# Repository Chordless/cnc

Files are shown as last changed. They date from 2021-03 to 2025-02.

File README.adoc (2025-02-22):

= The ERK-1 CNC
:toc: preamble

Designing, building & blogging a small desktop CNC.

.Current machine status
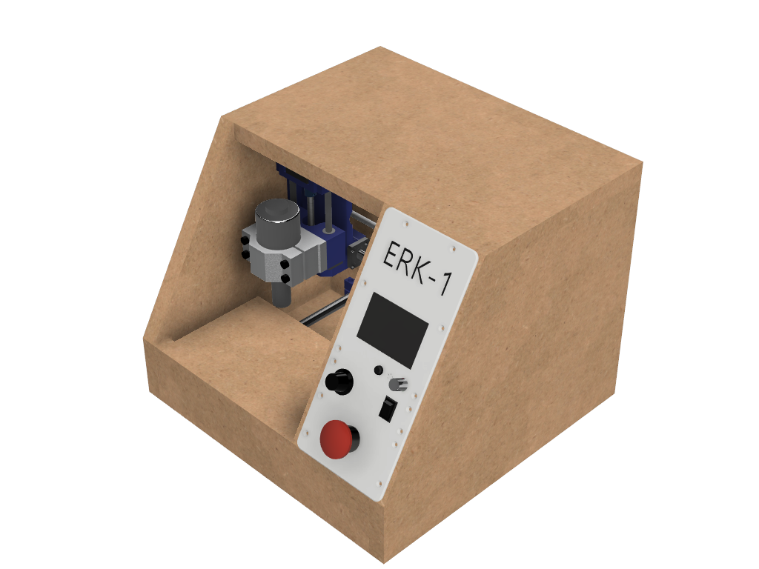
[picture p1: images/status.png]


== What's going on here then?
I'm designing a tiny desktop-friendly CNC. This repository will contain the design files, and I'm also blogging about the project in this readme file.

== Why yet another CNC design?
There are lots of great, free-to-build CNC designs already in existence on the internet. But, there is one particular type of CNC machine that I simply have not found any DIY designs for: The desktop micro mill. Think of those machines dentists use to create dental prostheses. Fully enclosed, tiny CNC machines you can use in an office: not too noisy, and not spewing dust everywhere. Something you could use while living in an apartment for experimenting and learning about CNC, and then being able to stow it away under the desk when not in use.

== Goals
* Apartment friendly
  - Quiet _enough_. CNC cutting will never be silent, but I'm trying to keep it quiet enough that the neighbors don't call the cops.
  - Dust control. CNCs can spew out lots of fine wood dust, and this would be terrible in an apartment. The machine must be fully enclosed, have controlled negative air pressure and a filter for catching all the dust. It needs something like a built-in vacuum cleaner.
  - "Stow-able". It should all be contained in a single unit, that you can pick up off the desk and stow in a closet. This also means it must be light enough that one person can feasibly carry it.
* Inexpensive
  - I'm going for a price of around 300-400$
* Possible to build without another CNC / Laser cutter. Some parts will unfortunately require a 3D printer. The machine frame will be mostly made out of wood.
* As small a footprint as possible. I'm inspired by the amazingly small https://vorondesign.com/voron0[Voron 0] 3D printer, but will have to scale up a bit from that ideal.

== Non-goals
* Metal milling
  - Out of the question. Nope. Not doing it. This will be a machine that can cut wood, plastics and modeling foam.
* Big working area
  - Not a goal at all. The machine footprint will be tiny in DIY CNC terms, and the cutting area will be even smaller. I'm totally fine with a toy-like working area of 13 cm x 10 cm x 2 cm.
* Precision
  - It would be nice if a tiny mill could mill tiny parts accurately. But this one won't. I'll be using cheap parts. Hopefully some of the parts can be "upgraded" for those with a larger budget, without requiring a redesign of the machine. Like using proper brand name linear bearings instead of the bottom dollar stuff I will be using. The bearing form factor will still be the same.

== Machine specs

- Fixed-gantry CNC machine
- Machine outer dimensions: 40 cm x 40 cm x 35 cm
- Axis travel: 130 x 130 x 60 mm (X, Y, Z)
- 200W spindle
- Sensorless homing, all directions (X-,X+,Y-,Y+,Z-,Z+)
- Fully enclosed
- Integrated dust filter

== Bill Of Materials

=== Frame and fasteners
- 8x different woods panels. Dimensions will come later. Should be cut out of 22 mm thick sheets of fibreboard or MDF. Any wood should work as long as it is 22mm thick.
- TODO: Lots of m3 and m4 bolts and nuts
- TODO: Wood screws
- TODO: Threaded inserts
- 2x 300 mm lengths of DIN rail (you can get away with using 240 mm)

=== 3D printed parts
- TODO

=== Electronics
- Controller board: `MKS GEN_L V2.1`
- Stepper motor drivers: 3x `TMC2209 V1.2`. These are silent, have software controlled current settings and support sensorless homing. With these, the machine won't need limit switches.
- Steppers:
  * 2x large `NEMA 17` stepper motors. The X- and Y-axis motors will be stationary, and they can be larger (longer) than the Z-axis motor.
  * 1x normal-sized `NEMA 17` stepper motor for the Z-axis. This will be moving as part of the X-carriage, so it shouldn't be too heavy.
- LCD screen: `RepRapDiscount Full Graphic Smart LCD Controller`
- Wi-Fi controller and web UI: A `Raspberry Pi` running chilipeppr, cncjs, or similar program.
- Spindle Motor: https://www.aliexpress.com/item/32908212687.html[Chinese 200W ER11 spindle with bracket]
- Spindle motor power supply. Normally rated for 48V max output, often sold as a set with the spindle motor. Should also include a potentiometer for adjusting motor speed.
- 12V Power Supply. 100W or greater. Powers the motion controller, stepper motors and fan.
- 12V 1A+ 60mm *strong* fan. You want a really strong fan. Example: https://www.aliexpress.com/item/32792312541.html[60 mm Fan]
- Emergency Stop Button, 22 mm: https://www.aliexpress.com/item/32885416975.html[E-Stop Button]
- KCD1-101 toggle switch: https://www.aliexpress.com/item/32627544552.html[Toggle Switch] (For turning the spindle on/off)

=== Linear Motion
* Z-axis
  - 2x LMK8LUU linear bearings
  - 1x T8 flanged brass nut  (2 Leads, Pitch 2 mm)
  - 2x 8x125 mm linear rods
  - 1x T8x100 mm trapezoidal leadscrew (2 Leads, Pitch 2 mm)
  - 1x 608ZZ ball bearing ("skate-bearing")
  - 1x Rigid shaft coupling, 5 mm to 8 mm
* X-axis
  - 4x LMK12UU linear bearings
  - 1x T8 flanged brass nut (2 Leads, Pitch 2 mm)
  - 2x 12x238 mm linear rods
  - 1x T8x232 mm trapezoidal leadscrew (2 Leads, Pitch 2 mm)
* Y-axis
  - 4x LMK12UU linear bearings
  - 1x T8 flanged brass nut (2 Leads, Pitch 2 mm)
  - 2x 12x258 mm linear rods (Axis length undecided)
  - 1x T8x252 mm trapezoidal leadscrew (2 Leads, Pitch 2 mm)

=== Misc
- A vacuum cleaner bag for `Philips Geneva HR6995`. If you use a different vacuum cleaner bag, you will have to design your own holder for it.

== Update 1 - 2021-03-18

.Humble beginnings
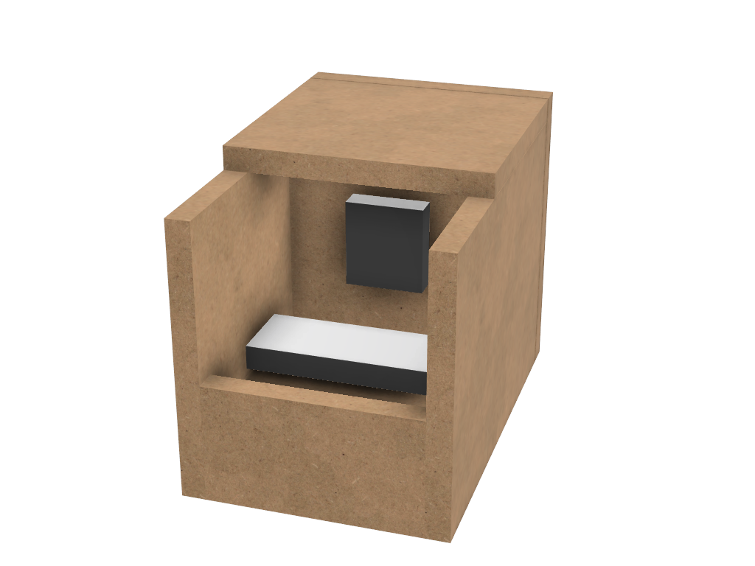
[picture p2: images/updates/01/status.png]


I've started sketching up the frame in Fusion 360. The rough design plan is:

- A cutting area in the upper front part of the machine.
  * Y-carriage moving from front to rear.
  * X-carriage moving from side to side
  * Z-carriage mounted on the X axis, moving up and down.
- A space under the machine for power-supplies etc.
- A space in the upper rear part of the machine for the motion controller and Raspberry Pi.
- A space in the lower rear part the machine for a powerful exhaust fan, and some kind of dust filter. Perhaps this will contain a vacuum cleaner bag, and literally work as a built-in vacuum cleaner.

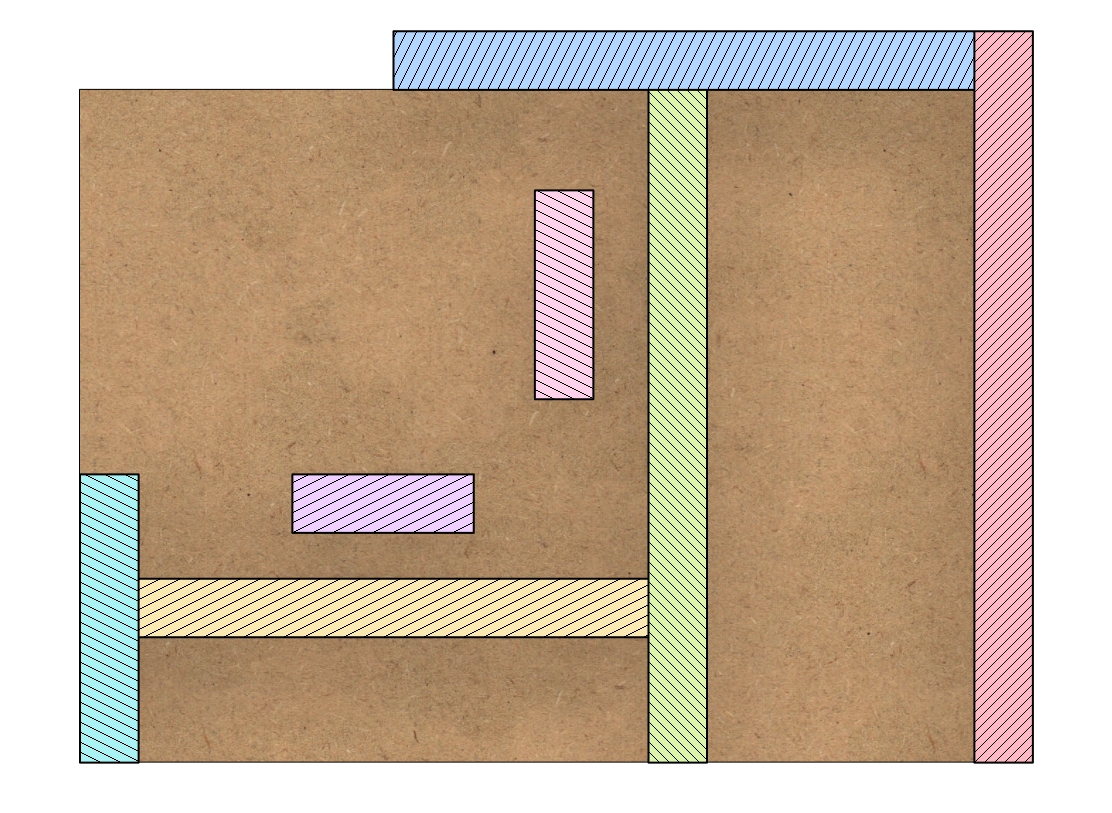
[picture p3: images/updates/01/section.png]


Eventually I realized that the shape and size of the frame is very dependent on the size and position of the spindle. I've made it my first goal to design the Z axis, and to make it as compact as possible. This will determine how small I can make the overall machine. As for the spindle, I'm currently designing for a 200W cheap chinese spindle motor. It seems small enough, yet should be able to cut small pieces of wood nicely.

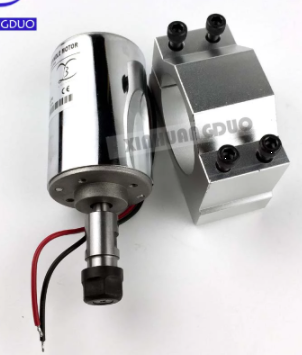
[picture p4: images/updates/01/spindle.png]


As part of the Z axis design, I'm making CAD models of some "standard" linear motion parts I expect to be using. I might even 3D print these models and use them as "mock" parts when prototyping the machine. I still haven't decided on the bearing form factors I will be using, and when I order them it will easily take one or two months before they arrive. Being able to assemble a "fake" version of the Z axis using plastic parts will probably be useful!

image:images/updates/01/LMK8UU v4.png[200,200]
image:images/updates/01/T8 Brass Nut v2.png[200,200]
image:images/updates/01/Spindle Clamp 52mm v2.png[200,200]
image:images/updates/01/Spindle 200W v2.png[200,300]

== Update 2 - 2021-03-19

.It's not easy being small
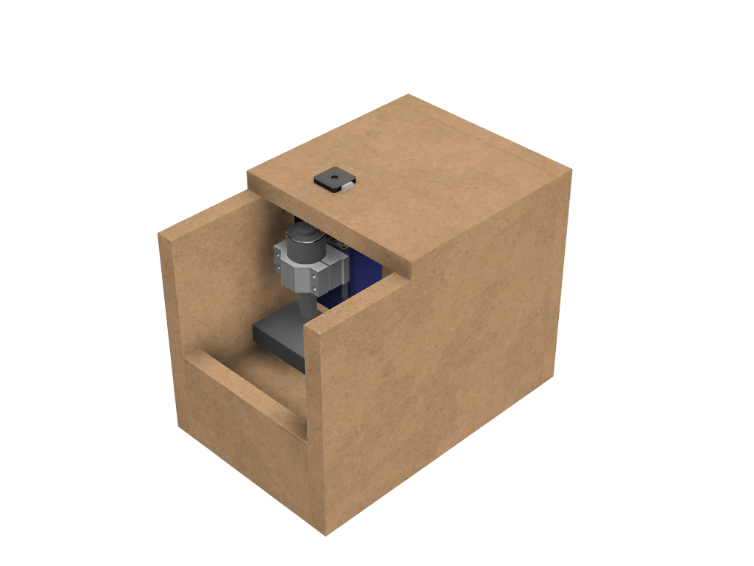
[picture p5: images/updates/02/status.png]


I've designed a first version of the Z-carriage and started on the X-carriage it rides on.
This machine is inspired by the tiny Voron 0 3D printer, which has _outside_ dimensions of 24 cm cubed. Right now my frame sketch has those _inside_ dimensions in the cutting chamber, so it's already larger than the Voron. And I've designed a Z-axis as small as I could without getting into weird tricks.

And yeah, that's the Z axis stepper motor poking through the top. _Oops._ I can expand the machine dimensions a bit more, but I don't want to go *that* big. I'll have to redesign these parts and save space wherever I can.

[discrete]
=== Z-carriage
The Z-carriage itself is pretty small. Most of it consists of the spindle mount bracket, and a small 3D-printed block to hold 4 bearings and a nut. If I'm sticking with a 52 mm diameter spindle, and the metal bracket, there's not much space that can be saved here.

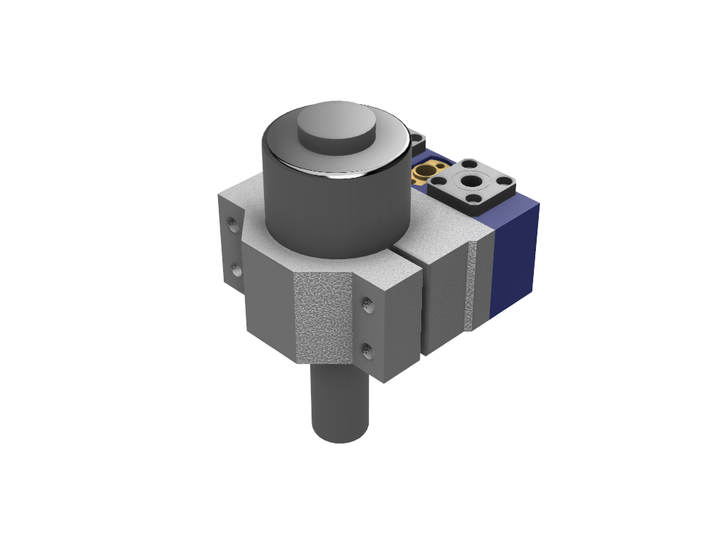
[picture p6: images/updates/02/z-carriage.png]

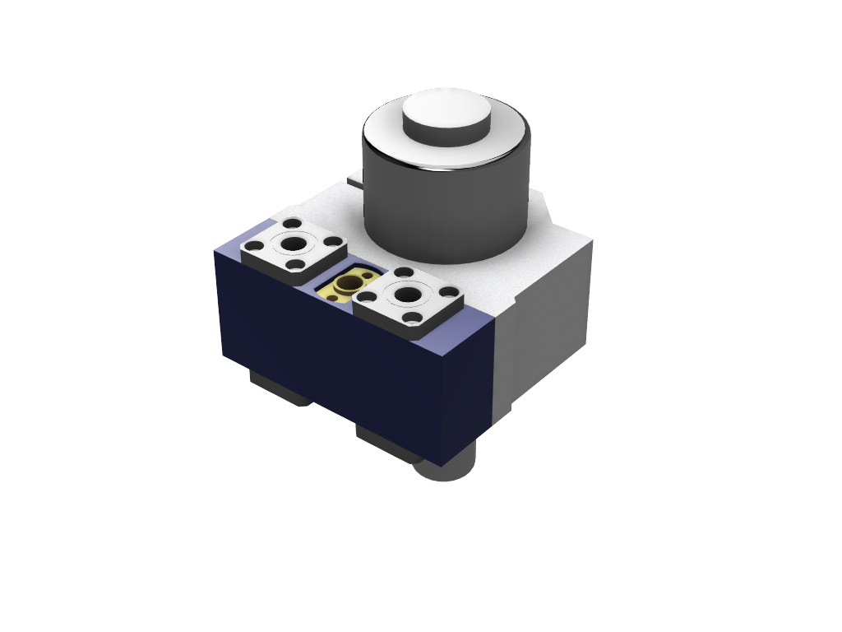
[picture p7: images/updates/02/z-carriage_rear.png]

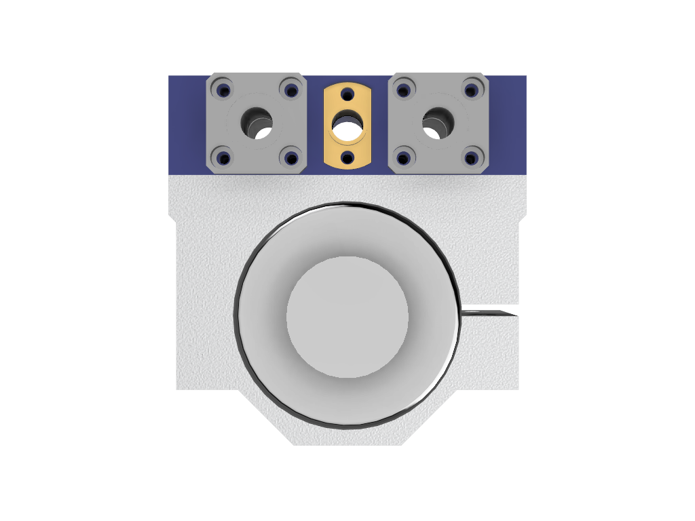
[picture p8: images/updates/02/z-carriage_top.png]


I actually don't want to use 3D-printed parts in this particular part of the machine. Anywhere but here. The spindle can get pretty hot, and that heat will creep into the 3D-printed block. I don't want to worry about my machine parts melting when I use the machine, so I'll have to pull some tricks here. Perhaps I can design in a sheet of plywood between the aluminium bracket and the 3D-printed block, as thermal insulation. We'll see.

[discrete]
=== X-carriage / Z-axis
The first X-carriage design is a simple box made from 3D-printed parts.
(The stepper motor and coupling don't quite line up with the brass nut in the z-carriage. I'll rework it later.)

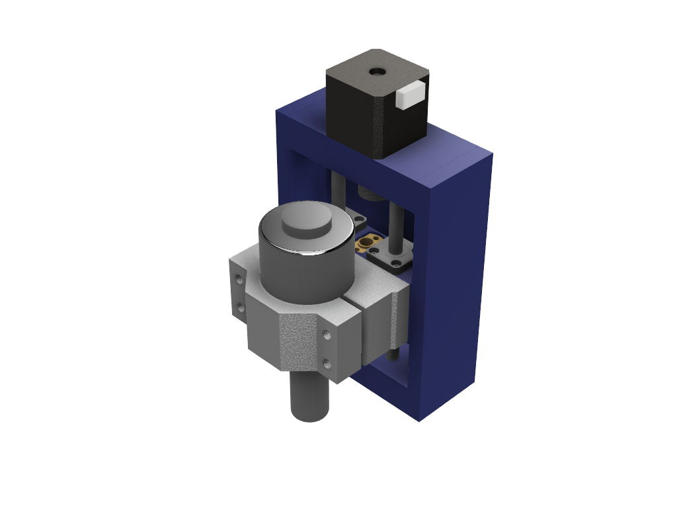
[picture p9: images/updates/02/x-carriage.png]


There's probably a bit of space to save here.

- The box sides aren't _necessary_. They do help with rigidity though.
- Perhaps the axis could be folded, using a belt drive, so that the stepper motor isn't on top. I don't know where else I want to put it though.
- The whole axis could be made shorter.

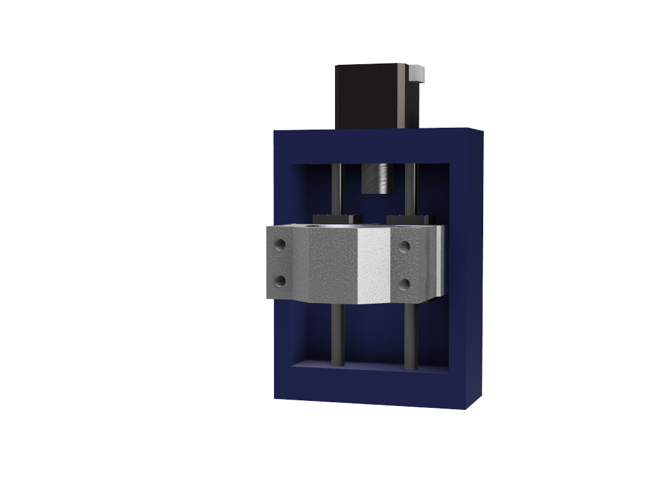
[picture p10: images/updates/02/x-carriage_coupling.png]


In this image, the axis is all the way up, at the end of it's 40 mm travel. The stepper motor shaft and coupling make me waste quite a lot of space. Without those, the box could be shortened, so the Z-axis bearings touch the top of the box in this position. If I choose a stepper motor with an integrated 100 mm leadscrew, instead of a regular shaft, I can save 30 mm of height here. That's probably too good to pass up.

== Update 3 - 2021-03-22

.Redesigned Z-axis
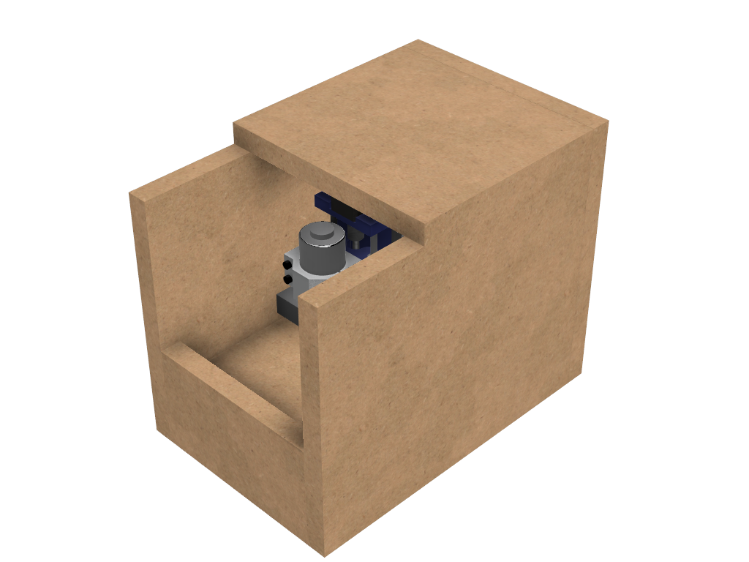
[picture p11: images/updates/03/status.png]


I managed to improve the Z-axis and shrink it down to something usable. I still had to increase the height of the machine a bit, but not that much.
Before and after shots of the Z-axis:


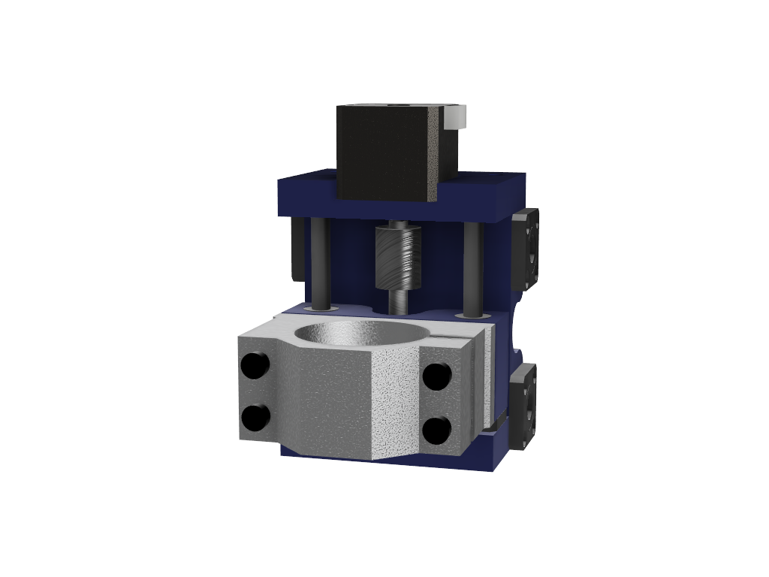
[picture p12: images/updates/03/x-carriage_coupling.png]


The images are not to scale, so it's not a perfect comparison. The box has been shortened a lot, and the plastic sides are gone. I added clearance for the stepper motor coupler to the Z-carriage part, so I don't have to use a special stepper motor with an integrated leadscrew after all. The Z-carriage now moves all the way up, so it touches the plate holding the stepper motor, and axis travel is still 40 mm.

The Z-axis and X-carriage is now complete, so I will print this version and see if things fit together as planned.

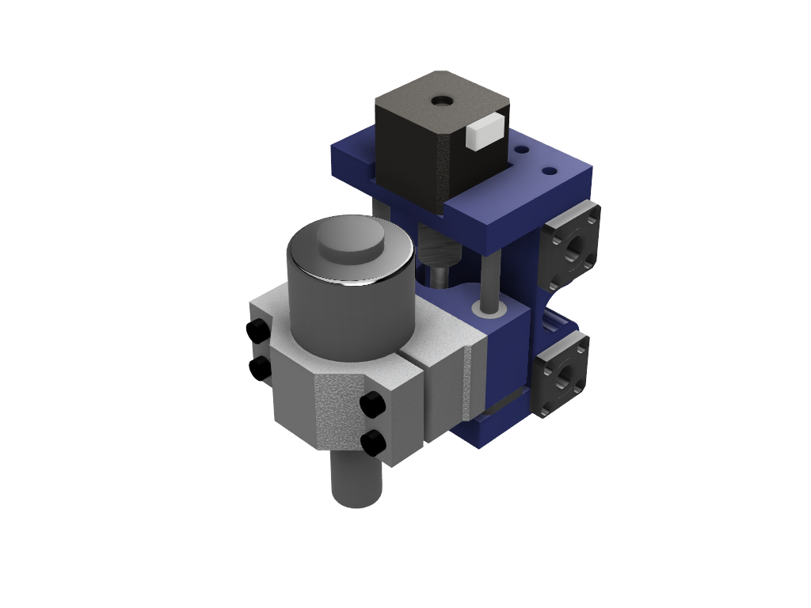
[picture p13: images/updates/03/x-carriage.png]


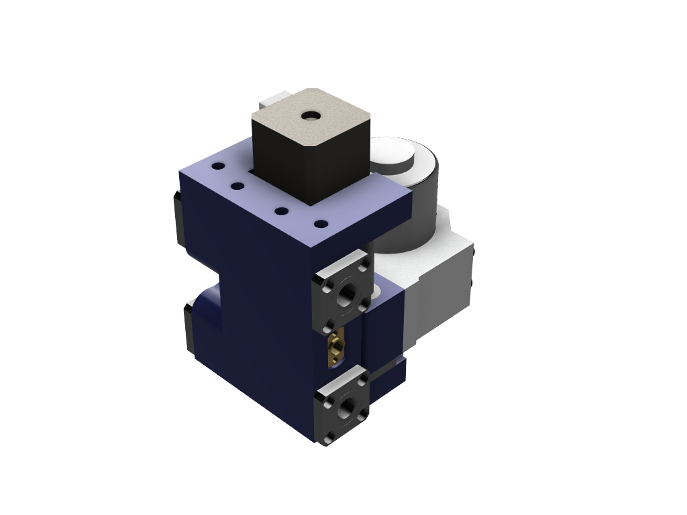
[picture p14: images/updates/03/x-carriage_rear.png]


I will also be liberally using "mock" parts for this test assembly, since no linear motion parts have been ordered from ebay yet. A bunch of more standard parts were modeled:

image:images/updates/03/mocks/608ZZ Bearing v2.png[,150]
image:images/updates/03/mocks/Flexible Coupling v2.png[,200]
image:images/updates/03/mocks/LMK8LUU v2.png[,250]
image:images/updates/03/mocks/LMK12UU v2.png[,270]
image:images/updates/03/mocks/NEMA 17 37mm v4.png[,300]
image:images/updates/03/mocks/NEMA 17 60mm v2.png[,300]

The next step of the design is to revisit the machine frame. I want to make some layout changes before properly designing in the X-axis.

== Update 4 - 2021-03-25

.Redesigned frame
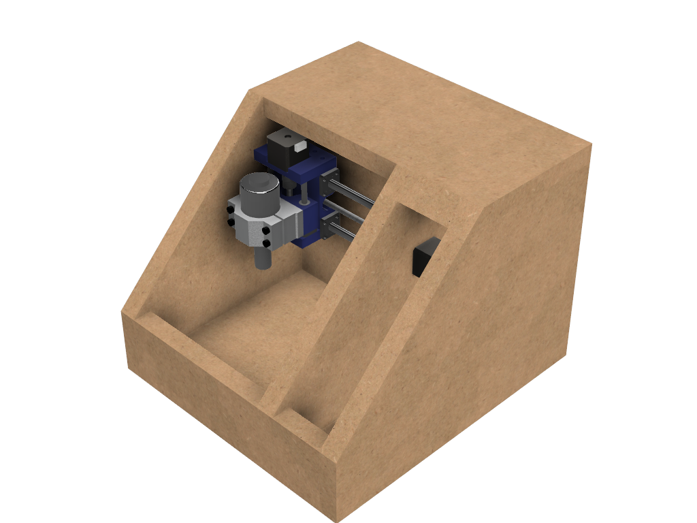
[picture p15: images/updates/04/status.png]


The frame has been redesigned, now it looks more like a usable machine. I plan to have a hinged plexiglas cover in front of the cutting area, and a 3D-printed panel on the right side. The right side panel will hold the LCD-display, emergency stop button, and probably a spindle speed control knob.

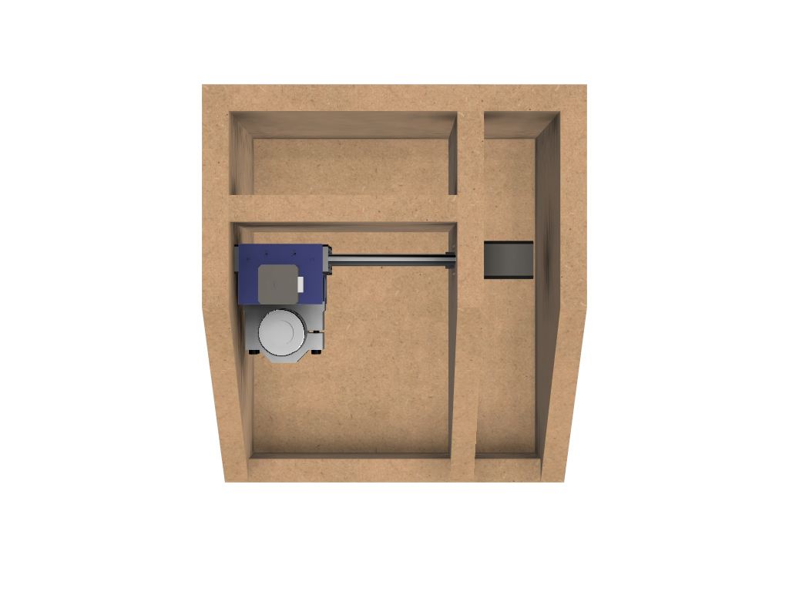
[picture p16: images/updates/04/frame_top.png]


The frame plan changed a bit:

- The cutting chamber is still on the front left side.
- There's no longer a power-supply chamber under the machine.
- The whole right side of the machine is now the electronics compartment.
 * (Hopefully I can fit all the controllers and power supplies here.)
- There is another chamber behind the cutting area, that I plan to use for dust management (an integrated vacuum cleaner).

Outside dimensions at this point are:  +
40 cm x 44 cm x 34 cm (width x length x height)

There is also now a complete X-Axis. The rods are held in halfway-trough drilled holes in the wooden side panels. I am unsure if this is a good idea, or if I should design some actual holders for the rods, that then bolt onto the side panels. On the other hand, that would eat up a couple centimetres of X-axis travel.

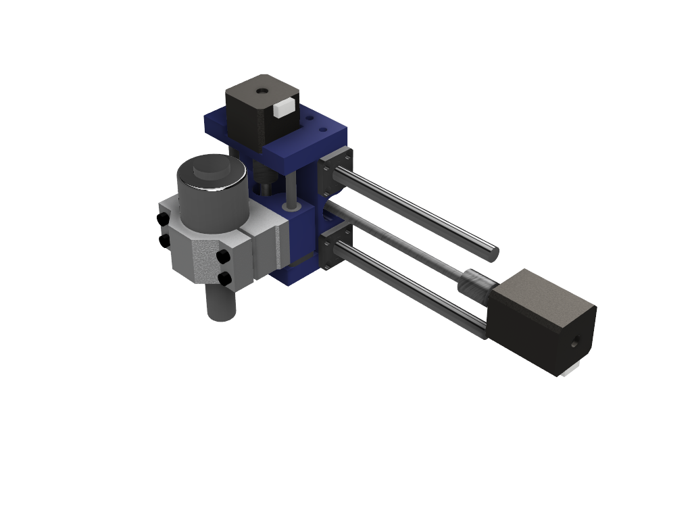
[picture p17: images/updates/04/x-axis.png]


Next step: The Y-carriage

== Update 5 - 2021-03-29

No real design update today. The Y-axis is in progress. I'll just be writing about electronics and 3D printed prototyping since I think it's neat.

[discrete]
=== Electronics
These are the motion electronics I plan to use (disregard the blue lab power supply at the top):

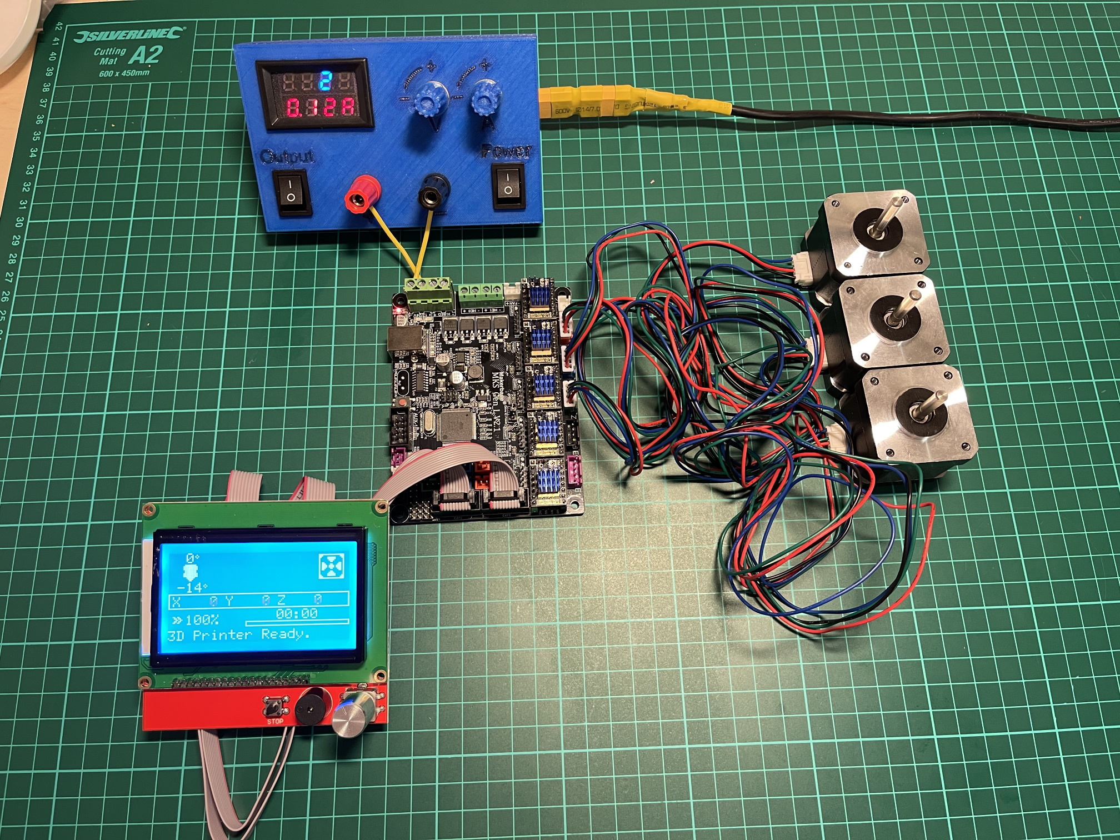
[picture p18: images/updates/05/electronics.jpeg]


The controller board is the `MKS GEN_L V2.1`. It's based on the 8-bit ATMEGA2560 CPU, quite common among 3D printer controller boards, and has nice inputs and outputs for the common things a 3D-printer needs. It's also quite easy to repurpose for driving a CNC.

The stepper drivers I am using are the `TMC2209`, and they should be very good in combination with this board. For one thing, the drivers make the steppers move very quietly. The stepper motor noise is not much compared to a cutting tool driving through wood, but every little bit helps. The board supports communicating with these drivers over UART, so the board can send configuration commands to the drivers, and get status updates in return. This lets us configure the stepper motor current in the firmware. For example, we can set the current of each driver to exactly 1400mA, instead of fiddling with a tiny potentiometer to try to achieve a similar result.

The stepper drivers can also tell the firmware when motors are unable to move as commanded; when they lose steps. This means we can let the machine home itself without using any limit switches. We just tell the machine to move as far as possible along, say, the negative X-axis. When the machine hits the end of its travel, the motors will stall, and the stepper drivers will let the controller board know. We can then mark the current X position as X=0. This also lets us do the same thing for the positive X direction, and the same for the Y-axis and Z-axis. This is normally not supported on such machines, as positive homing would require 3 extra limit switches, in addition to the regular 3 switches used for homing each axis to zero.

The plan is to use this for usability improvements in the machine. Like automatically homing each axis to the positive direction after a cutting job. This would move the spindle up and to the right (out of the way), while pushing the Y-carriage towards the user. Which is nice.

[discrete]
=== Prototyping
I have printed a prototype of the Z-carriage and X-carriage. The parts printed in white are "real" machine parts; I intend for these to be 3D-printed in the final machine. The blue parts are just stand-ins; these are supposed to be standard linear motion parts that will be ordered when the machine design is complete. I already had these modeled to help with the CAD design of the machine, so it didn't take much extra work to get them 3D-printed.

.Z-axis all the way down
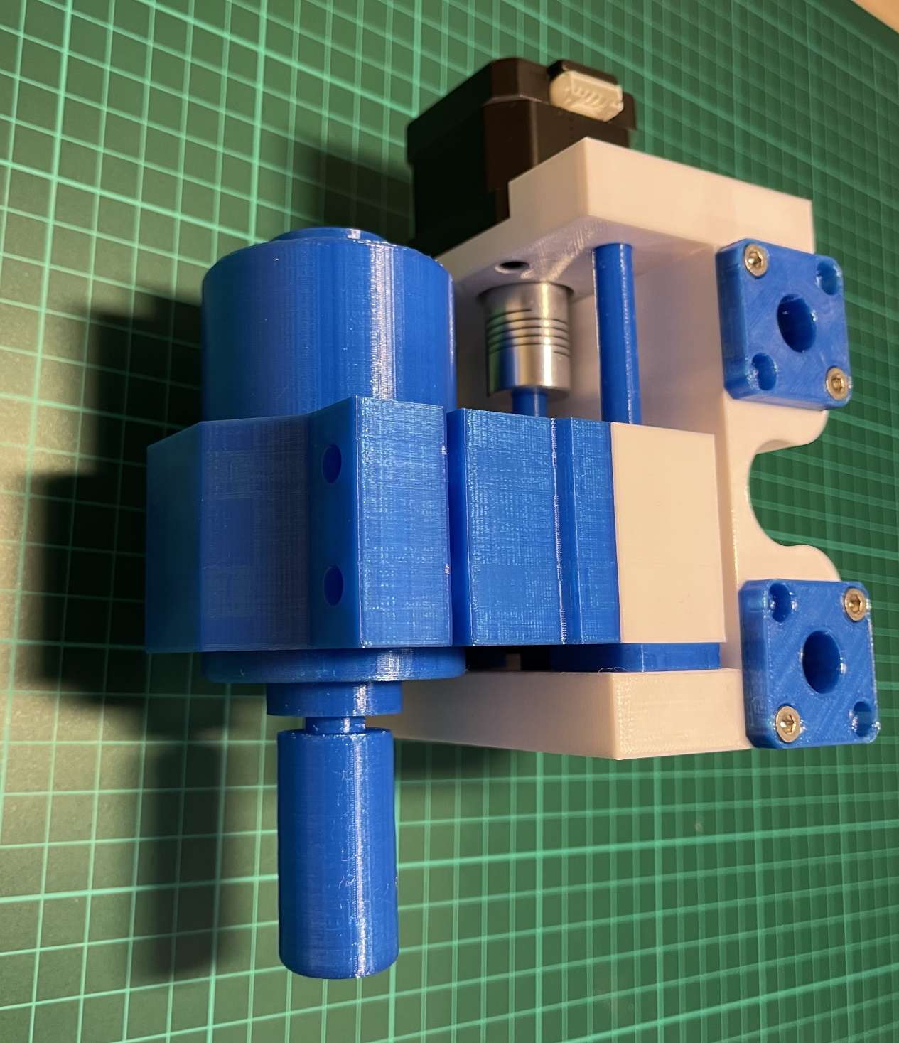
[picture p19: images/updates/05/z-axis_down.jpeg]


.Z-axis all the way up
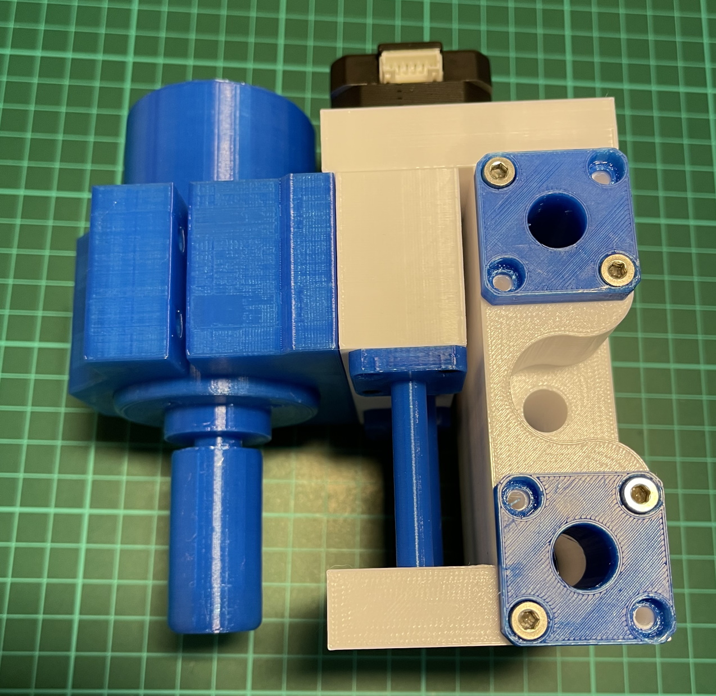
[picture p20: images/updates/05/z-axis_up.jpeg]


.Z-carriage with mock spindle and motor mount
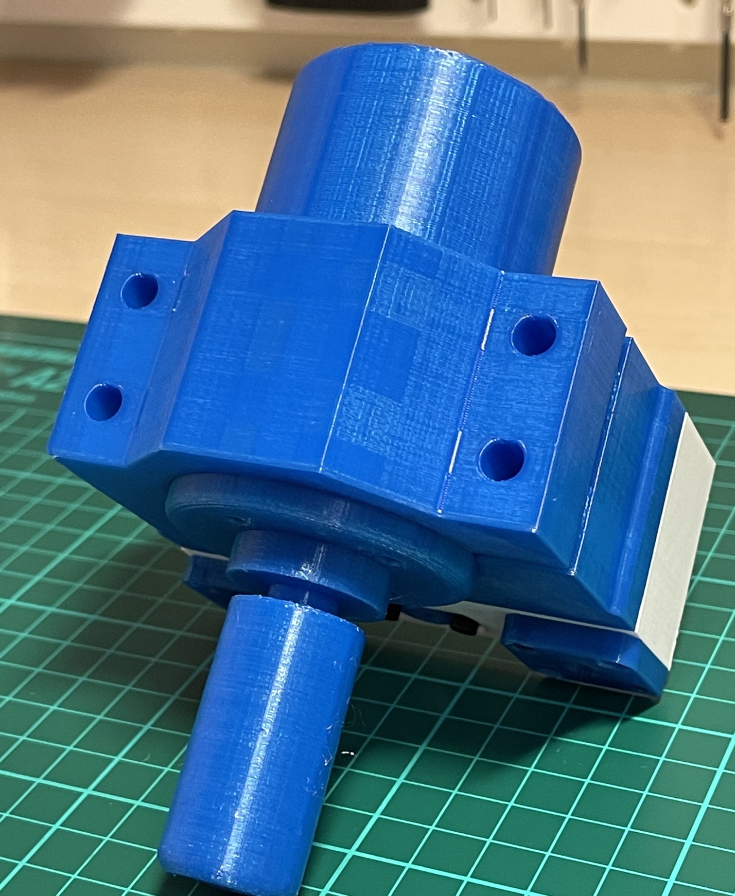
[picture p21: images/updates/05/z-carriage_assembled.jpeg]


.Z-carriage with mock spindle and motor mount, disassembled
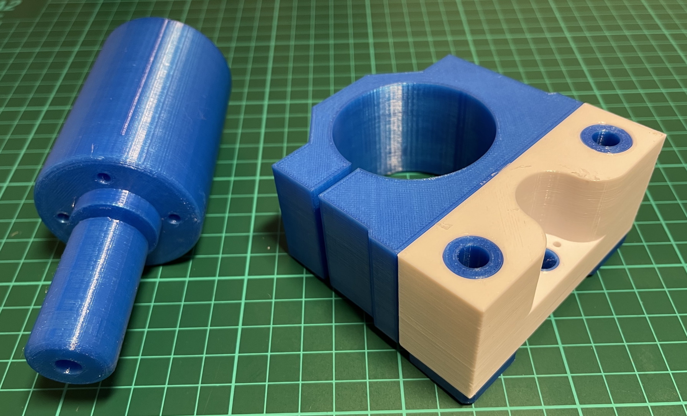
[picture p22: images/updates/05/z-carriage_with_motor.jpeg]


Prototyping like this is not only *fun*, but also lets me get a feel for the assembly of these parts, and catch problems early. Assembly went ok this time, there were no inaccessible screw-holes or such things. I found a few things I want to change though.

The current X-carriage consists of two parts: A large base part, and a top plate (holding the stepper motor) that screws into it from the top.

.Full Z-axis (Z-carriage and X-carriage)
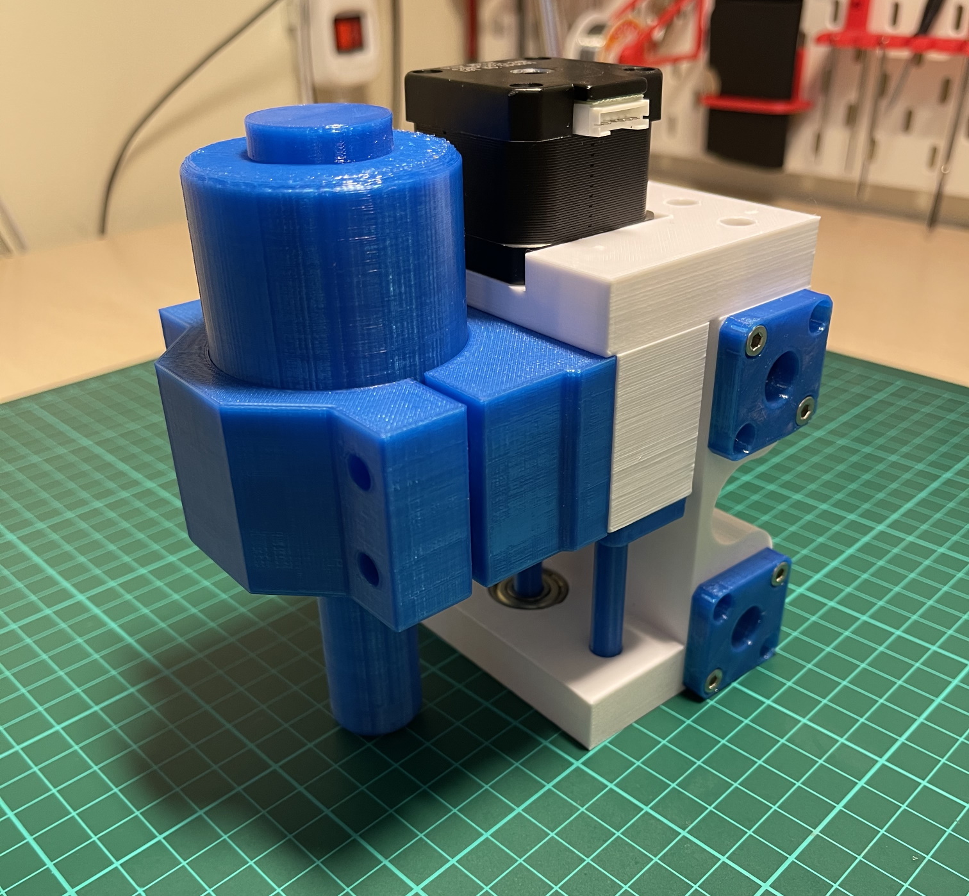
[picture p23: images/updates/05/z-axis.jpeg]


I was hoping the screws would hold these two pieces tightly together and in alignment. After seeing it in real life, I don't think the screw connection is strong enough. I will probably redesign the X-carriage to be a single part. This also lets me push the top X-rail higher up on the X-carriage, giving a longer distance between the X-axis rails. This is generally a good idea, mechanically.

I also think I can save a centimeter or two in the width of the X-carriage. The width of the Z-carriage is more or less defined by the width of the motor mount; this doesn't need to carry over to the X-carriage. At the very least the linear bearing flanges don't need to stick out of the sides of the X-carriage. This gives less distance (left to right) between the X-rail bearings, which is not a good idea mechanically. The upside is that it would give me more X-axis travel without increasing the width of the machine.

== Update 6 - 2021-03-31

.All 3 axes designed
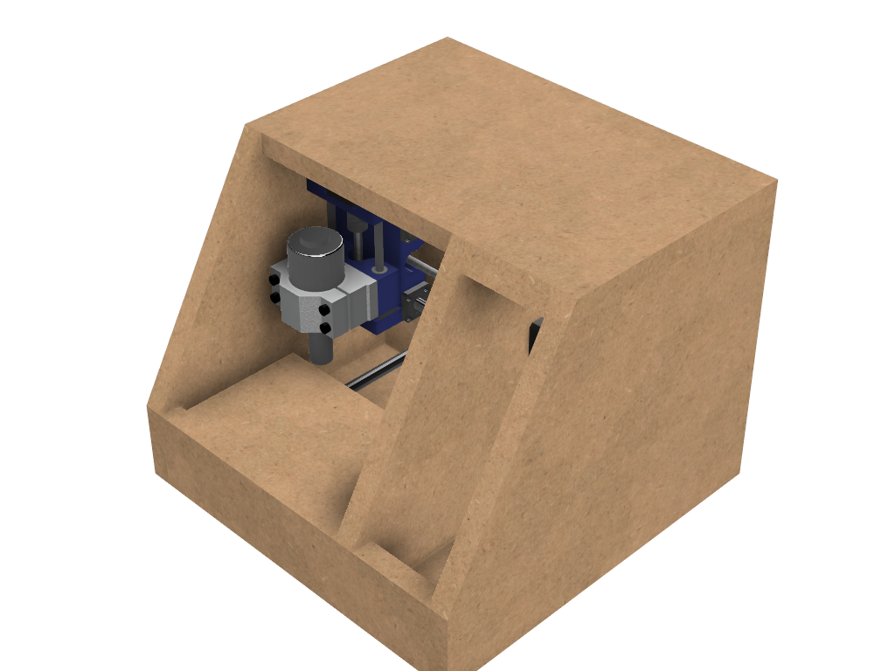
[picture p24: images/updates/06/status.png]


The machine now has a Y-carriage and Y-axis! Once all the three axes were in place, lots of small adjustments happened.

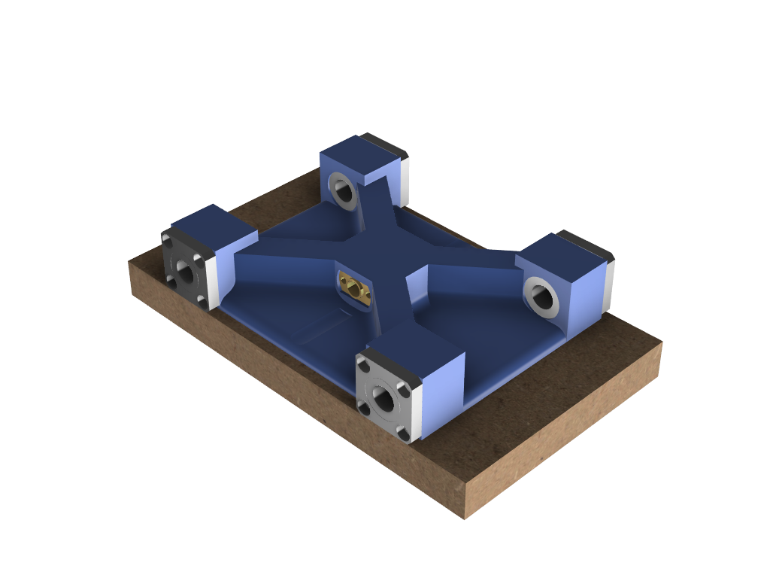
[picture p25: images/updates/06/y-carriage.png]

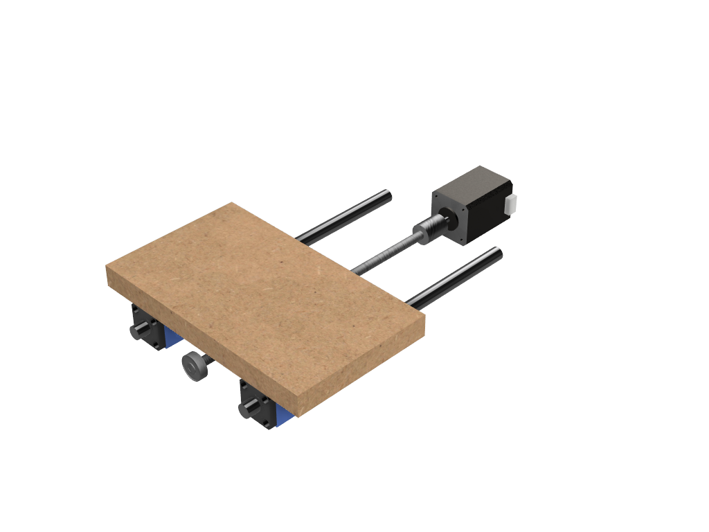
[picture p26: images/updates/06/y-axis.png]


- The X-axis was aligned, so the cutting tool is in the middle of the Y-axis.
- The angle on the front of the frame was changed from 45 deg to 30 deg. The top of the spindle motor could collide with the front plexiglas without this change.
- I also increased the Z-axis travel from 40 mm to 60 mm. This is just to ensure the Z-axis has enough clearance, even when using long or short cutting tools. In practice the thickest material you will be able to work with is still only 20-30 mm.

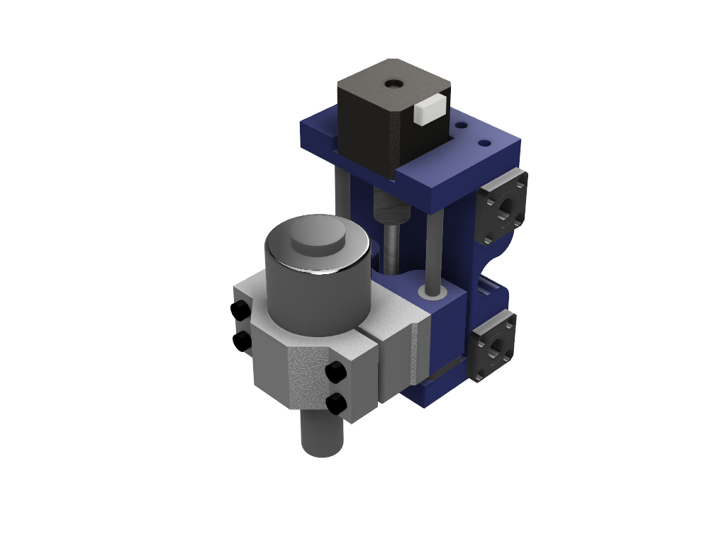
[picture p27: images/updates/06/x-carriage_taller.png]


So far I've been designing the frame with a 28 mm material thickness. The MDF wood sheets I will be using are actually 22 mm thick, so I updated the model to match this. The machine outer dimensions became slightly smaller as a result. Right now the machine dimensions are 396 x 396 x 324 mm (width, length, height). The machine travel is 138 x 130 x 60 mm (X, Y, Z). The model is parametric, so I can change this at will, but I'm currently trying to make the machine fit inside a 40 cm cube.

Axis travel *will* decrease in the future, since I've decided to change how the linear rails and screws mount to the frame. They are currently designed to fit inside halfway-through drilled holes in the frame sides. The positions of these drilled holes are absolutely critical, and if a hole is off by a fraction of a millimeter the axis will bind up instead of moving smoothly. I want the machine to be easy (and not require a CNC) to make, so this will not work.

I will be designing some 3D-printed "cassettes" to hold the rails and leadscrews, and these can be screwed (as a unit) inside each side of the frame. This will eat up maybe 2 cm of travel on the X and Y axes, but I think it is a necessary change.

At this point I could go on to modeling the electronics and filling out the electronics compartment, but I have quite a few things I want to refine and adjust in the cutting part of the machine first.

== Update 7 - 2021-04-04

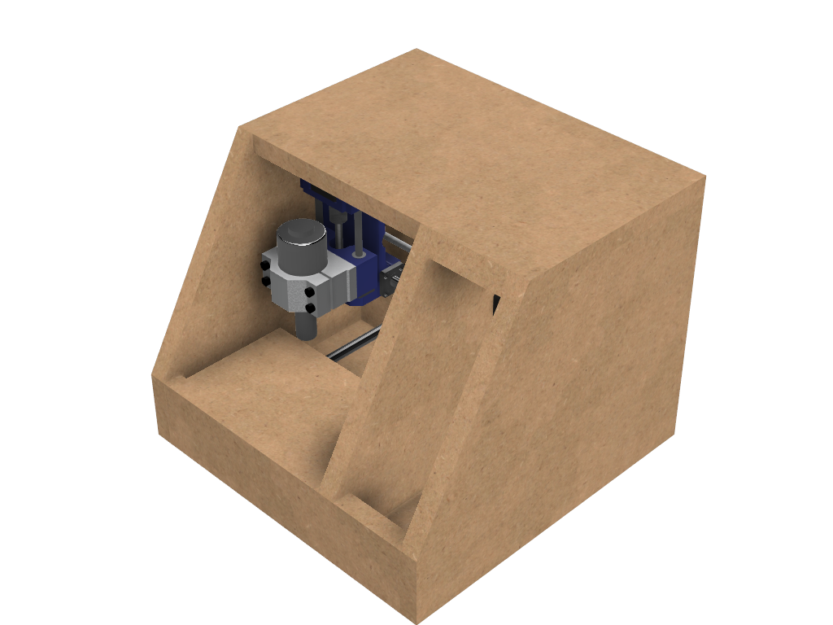
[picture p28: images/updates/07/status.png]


The changes are hardly visible in the machine frame image, but I have been reworking some details in the Z- and X-axes.

The X-carriage is now a single 3D-printed part. It also has some large cutouts at the back to reduce plastic usage and printing time. Hopefully it will still be strong enough for the machine. The Z-axis linear rails now insert from the top, and get clamped in place with a bolt and nut. The X-carriage has also been slimmed down a bit, gaining 12 mm of X-axis travel.

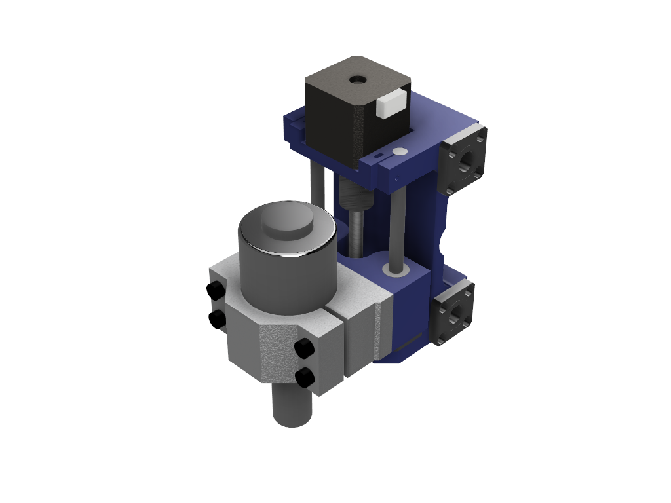
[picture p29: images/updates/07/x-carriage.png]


The X-axis also has some changes: The "cassettes" or mounting blocks have been designed. These ensure that the X-axis linear rails and leadscrew are parallel to each other. These blocks still have to be bolted to the frame sides with some precision, so the linear rails are perpendicular to the frame, but hopefully this is doable by hand.

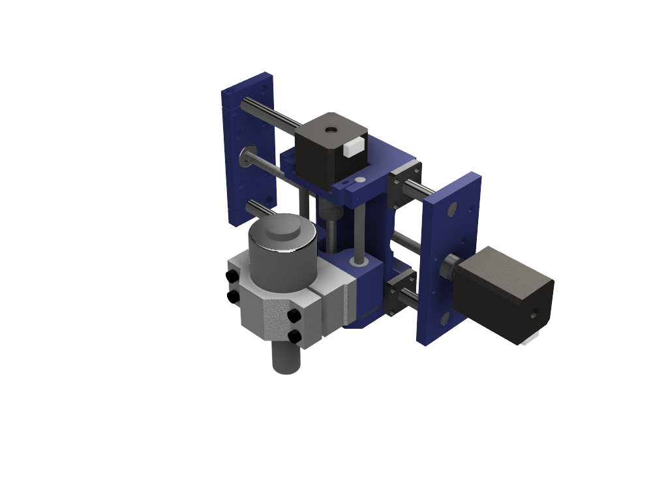
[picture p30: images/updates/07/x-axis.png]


Each of the mounting blocks are 10 mm thick, so in the worst case they eat up 20 mm of axis travel. In combination with the slimmer X-carriage, X-axis travel was only reduced by 8 mm. Not too bad!

With some luck, I will be able to add these mounting blocks to the Y-axis without affecting travel at all. I can just make the Y-carriage 20 mm shorter, underneath the spoilboard, to compensate.

Next up: The Y-axis also needs a pair of these mounting blocks.

== Update 8 - 2021-05-02

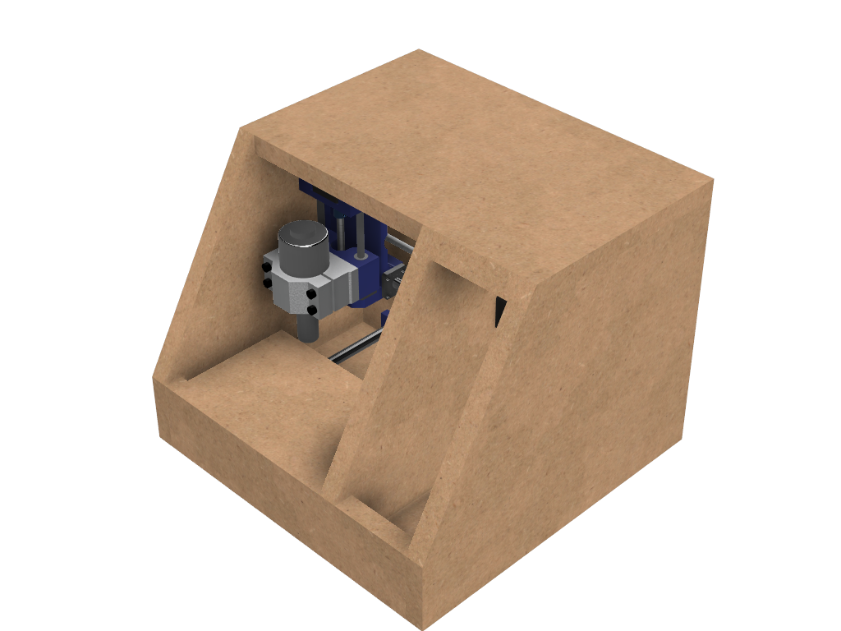
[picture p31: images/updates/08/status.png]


I have taken about a month of hiatus from the project. Linear motion parts were all ordered in the meantime, and I expect the last packages to arrive next week. Soon I can do test fitting with real parts. This time I finished up the "cassette" design, so the Y-axis now has a pair of mounting blocks for holding the linear rails and leadscrew. This means the cutting chamber of the machine is fully designed (or, at least the first version of it). Things will probably still change as I start building the machine and find out where the snags are.

.Y-axis with mounting blocks
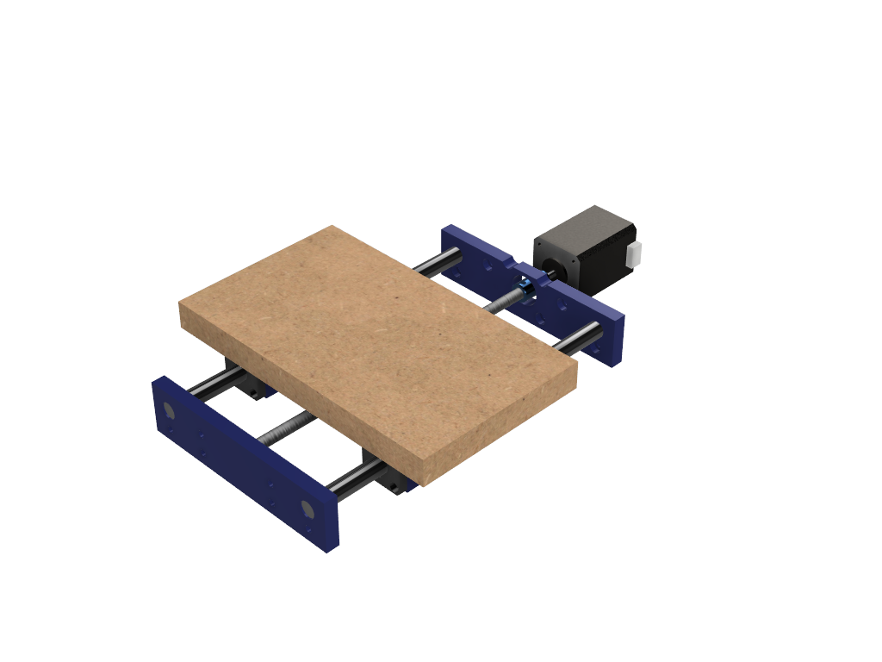
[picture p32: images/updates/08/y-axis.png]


Other minor adjustments:

- Switched over to using rigid couplings between stepper motors and leadscrews, on all axes. The design still has clearance for the larger flexible type couplings, for those who want to use that.
- Improvement to ease assembly: the Z-axis leadscrew can now be inserted/removed through a hole in the bottom of the X-carriage. You no longer need to remove the Z-axis stepper motor to get at it.

== Update 9 - 2021-05-16

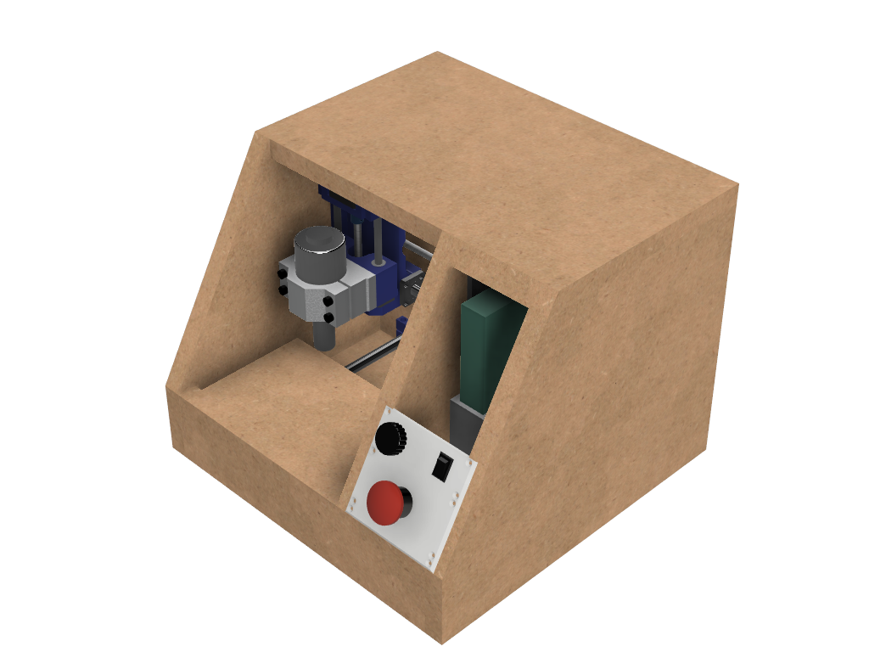
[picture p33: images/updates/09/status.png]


Lots to share this time. I've been working quite a bit on the project without updating. Most of the changes are subtle. Parts in the cutting chamber have been printed, improved, and reprinted. Practically every 3D-printed part was updated.

[discrete]
=== Prototyping

The mounting blocks I designed earlier had an unexpected side benefit. They allow me to assemble and test-fit the X- and Y-axes. I didn't think I would be able to assemble so much of the machine before building the wooden frame.

.X- and Z-axis assembly. Linear rods for the Z-axis in the background; they haven't been cut to length yet.
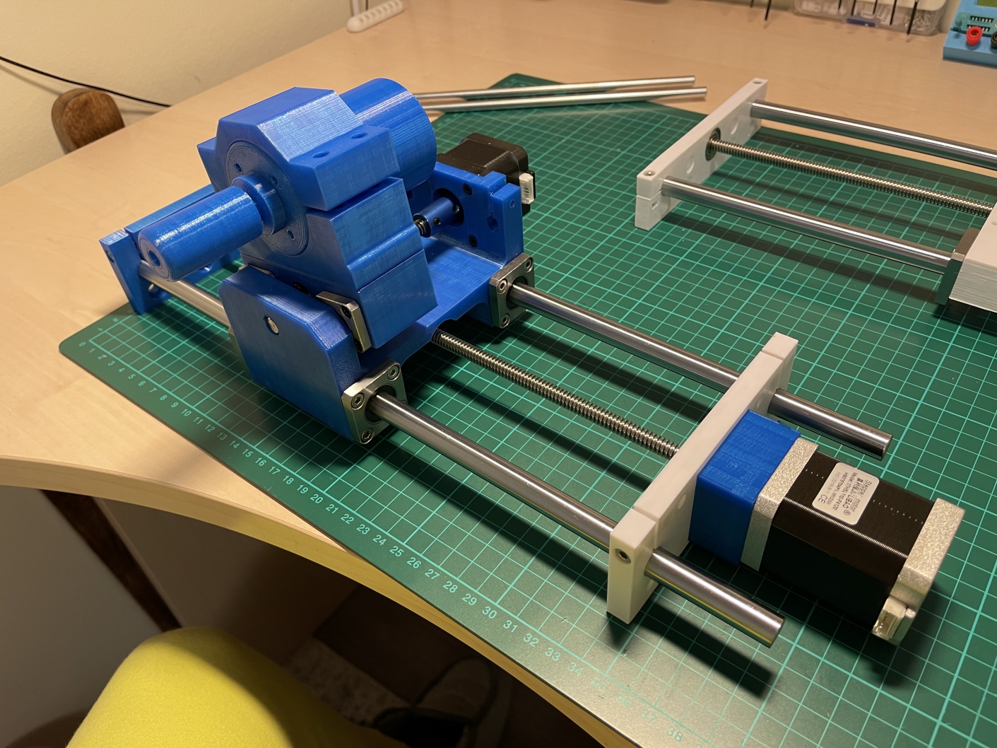
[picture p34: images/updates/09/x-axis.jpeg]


.Y-axis assembly. The blue square is a stand-in for the spacing the wooden frame will give the motor.
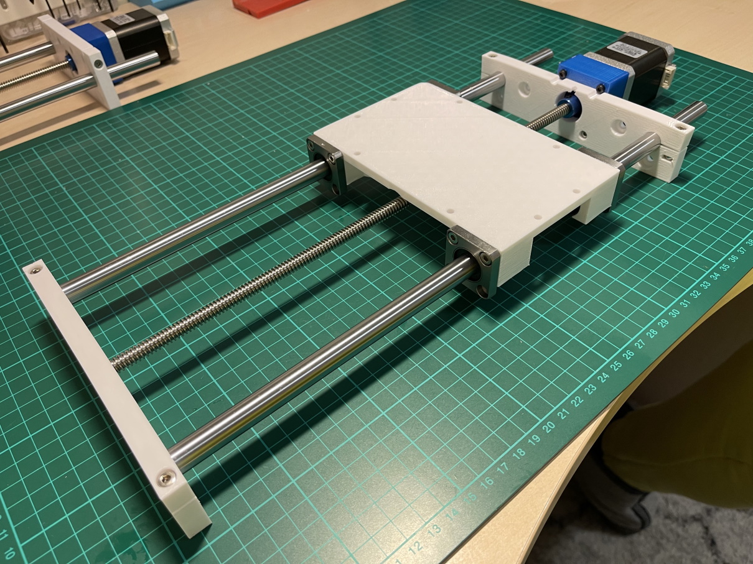
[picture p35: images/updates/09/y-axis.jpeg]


.Both axes
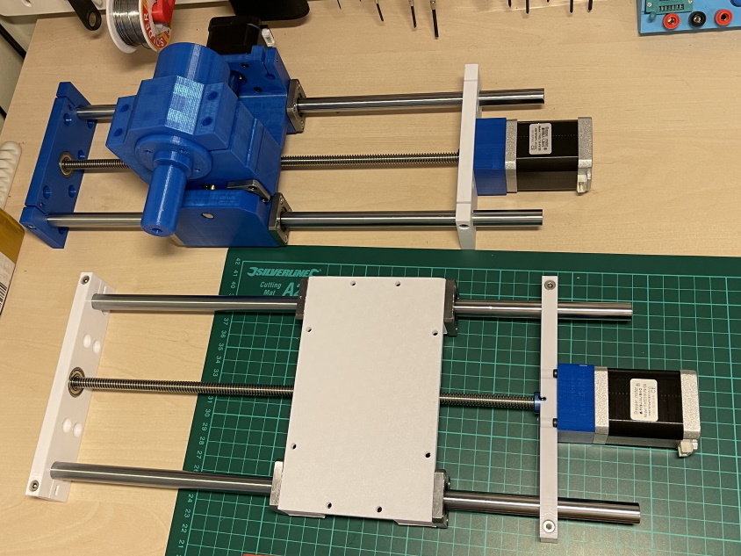
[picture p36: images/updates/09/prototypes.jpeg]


Note that the axes in the photos above are about 10 cm longer than what will be fitted on the final machine. I'm holding off on cutting the rods to length for as long as I can. It would not be cool if I shortened these 400 mm rods to 240 mm, and a design change forced me to make the rods 260 mm instead.

[discrete]
=== Electronics compartment

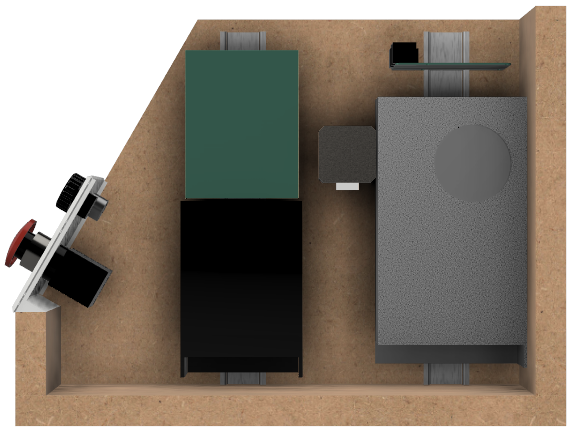
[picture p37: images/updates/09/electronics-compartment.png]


I've made a layout for the electronics compartment. It will contain quite a few things:

- 12V PSU (grey) - large psu, supplies power to most things
- 48V PSU (black) - powers the spindle motor
- MKS GEN_L V2.1 (green) - motion controller
- Raspberry PI 3 or 4 (upper right) - sends commands to the motion controller
- Whatever other parts are sticking into this chamber
  * X-axis stepper motor
  * E-stop from the front panel
  * LCD display from the front panel (not modeled yet)

The general plan is to mount two pieces of DIN-rail in this chamber, and let the electronics hang off of that. DIN-rails are usually not used vertically like I'm doing here. I'm hoping that I will be able to 3D-print any clamps or spacers needed to make it work.

[discrete]
=== Control Panel

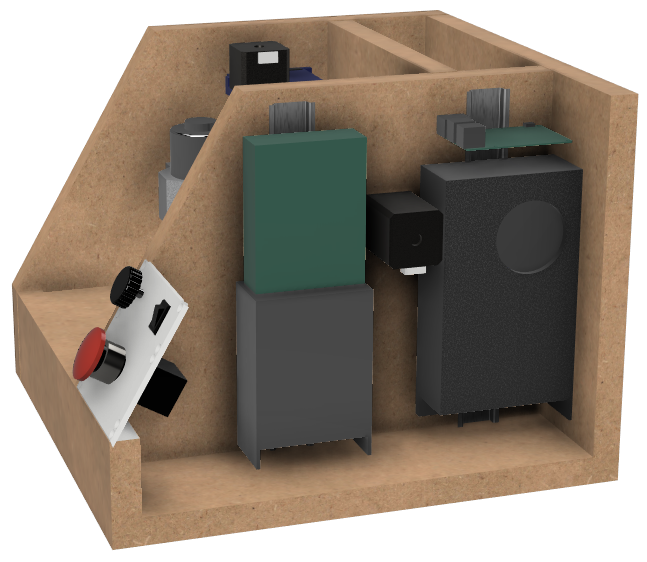
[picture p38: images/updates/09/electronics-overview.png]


I've started designing the control panel. It will occupy the right side of the front of the machine. It's made up of different modules that fit into the slot, held in place by wood screws.

.Planned modules:
- E-stop holder
- Spindle control panel (speed knob, on/off switch)
- LCD panel (using a display module common in 3D-printers)
- Spacer (just a blank panel to take up the rest of the space)

Next steps: Completing the control panel. Maybe starting work on the "vacuum cleaner" part, behind the cutting chamber?

== Update 10 - 2021-06-06

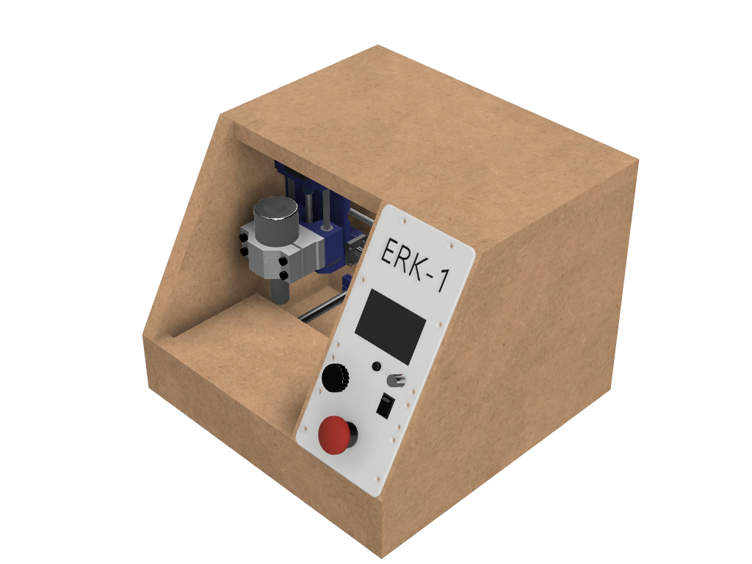
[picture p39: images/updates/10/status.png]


The front control panel is completed.

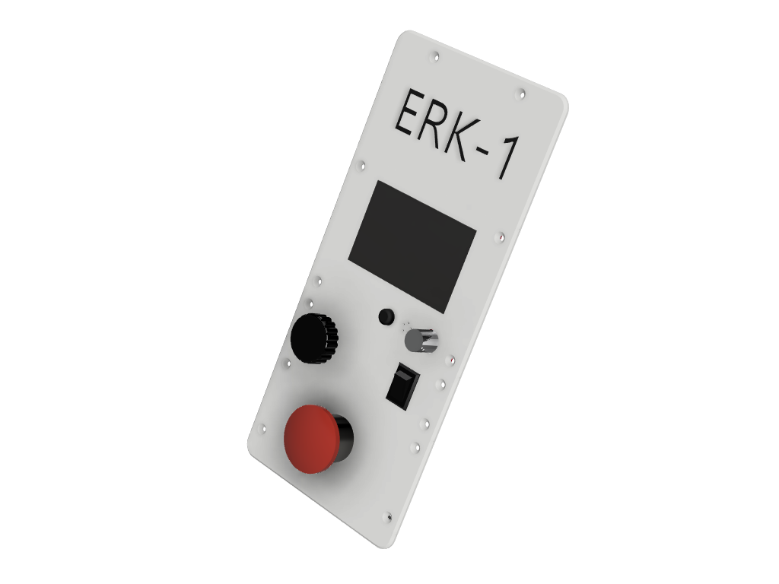
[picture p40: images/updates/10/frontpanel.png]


It contains these modules, from the top:

 - Top plate with model number. Just filling up the extra space that was available.
 - LCD display and controller: Holds the RepRapDiscount Full Graphic Smart Controller.
 - Spindle control: Spindle speed potentiometer and on/off switch.
    * This module might be unnecessary, if I can get the firmware and motion controller to manage the spindle motor for us. It will at least be present in the first version of the CNC.
 - Emergency stop button. I have not decided if I want to wire this up to kill all power to the machine, or to just have it cut power to the spindle motor.
 - Bottom plate.

[discrete]
=== Remaining

Most of the machine has now been designed! These are the things I can think of that are remaining:

 - Vent holes.
   * I plan for outside air to get sucked into the electronics compartment, through the cutting chamber, and then being exhausted through the vacuum cleaner.
 - The vacuum cleaner module itself
 - A hinge and handle for the front plexiglas sheet.
 - A jig for locating screw holes. This will help assemble the wooden frame parts.

== Update 11 - 2021-06-12

.No visible changes from the front.


This time I have designed the vent and "vacuum cleaner" system I wanted. This will use a single fan both for cooling and dust filtering. The plan is for this fan to spin slowly whenever the machine is on, to ensure airflow around the electronics. When the machine starts cutting, the fan should ramp up to full power to suck away as much cutting dust as possible. The air is filtered through a common vacuum cleaner bag behind the cutting area. The air takes a long route, through the whole machine:

.Machine air intake on the left, exhaust on the right.


.Intake upper right, exhaust to cutting chamber lower left.


.Intake lower right, exhaust to vacuum cleaner behind the X-axis.


.Air gets sucked through a common vacuum cleaner bag, mounted above the Y-axis stepper motor.


.Air is finally exhausted through the rear of the machine by a powerful 60 mm fan.


That's the plan for handling both cooling, and dust produced by the machine. It's a lot of work for a single 60 mm fan. We'll have to see if can handle the job, once the machine is built and running.

For reference, the vacuum bag holder I have designed is for a Philips Geneva HR6995 vacuum cleaner. I'm hoping that's a common type of vacuum cleaner bag, that can be sourced anywhere. If this turns out not to be the case, it should be easy to switch to another type of bag. Perhaps I will create several variants of the vacuum cleaner bag holder.

I finally received the last machine parts I lacked: The spindle motor, motor clamp and motor power supply. Things are rapidly approaching the stage where I can assemble the first version of the machine. The main blocker right now is that I need to manufacture the wooden panels for the frame. These need to be cut to the correct dimensions, and they need to be cut squarely. I have tried some test cuts with the woodworking tools I have on hand, and the results weren't good enough. I think I will need access to a table saw to be able to properly cut the machine frame.

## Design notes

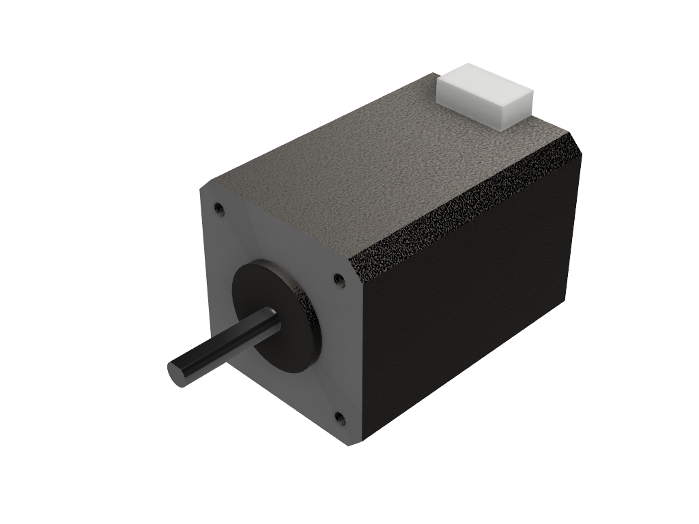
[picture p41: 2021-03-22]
images/updates/03/mocks/NEMA 17 60mm v2.png

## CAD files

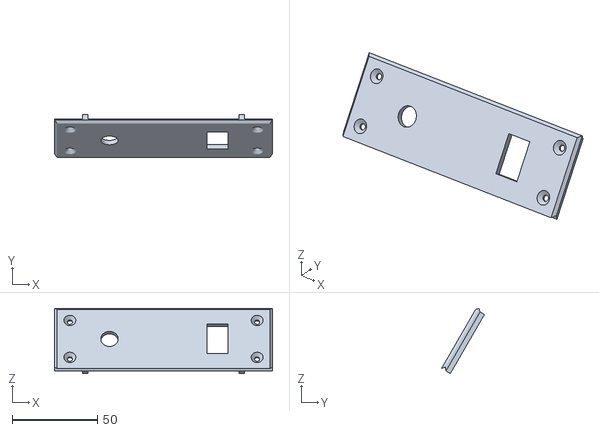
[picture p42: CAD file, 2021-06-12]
src/STL/controlpanel/Spindle Control.stl
127.8 x 25.2 x 38.2

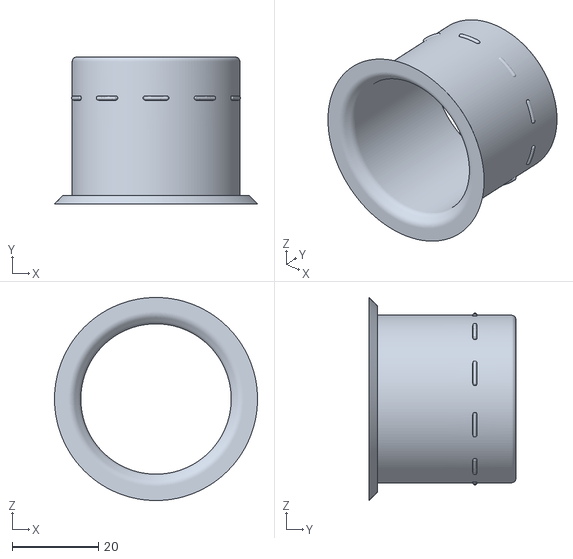
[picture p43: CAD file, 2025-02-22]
src/STL/extras/Vacuum Hole Plug.stl
47.0 x 34.0 x 47.0

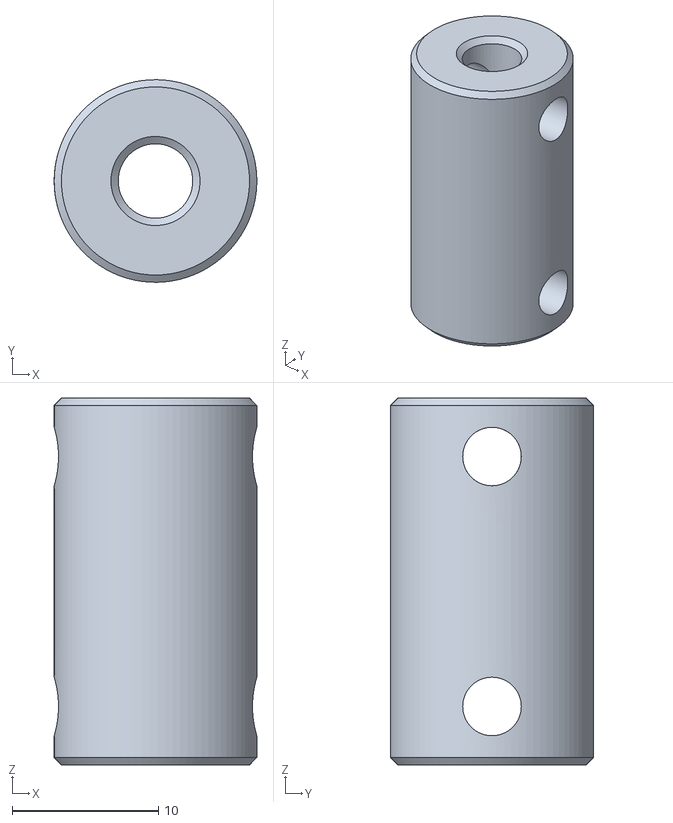
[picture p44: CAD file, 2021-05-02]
src/STL/mocks/RigidCoupling5to8mm.stl
13.9 x 13.8 x 25.1

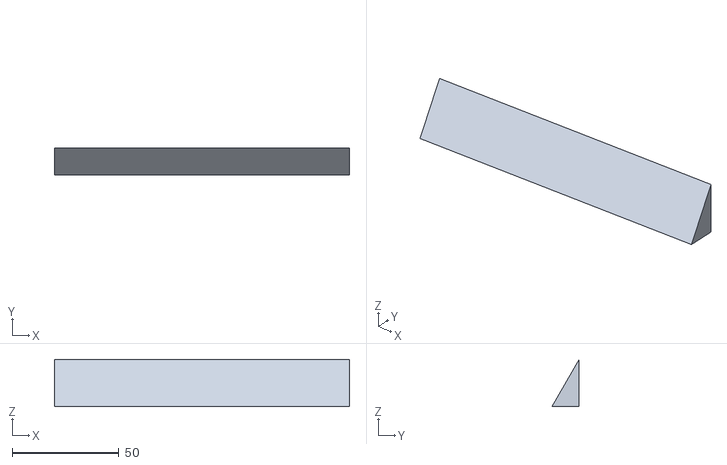
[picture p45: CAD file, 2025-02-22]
src/STL/shims/Top Right Angle Shim.stl
138.0 x 12.7 x 22.0

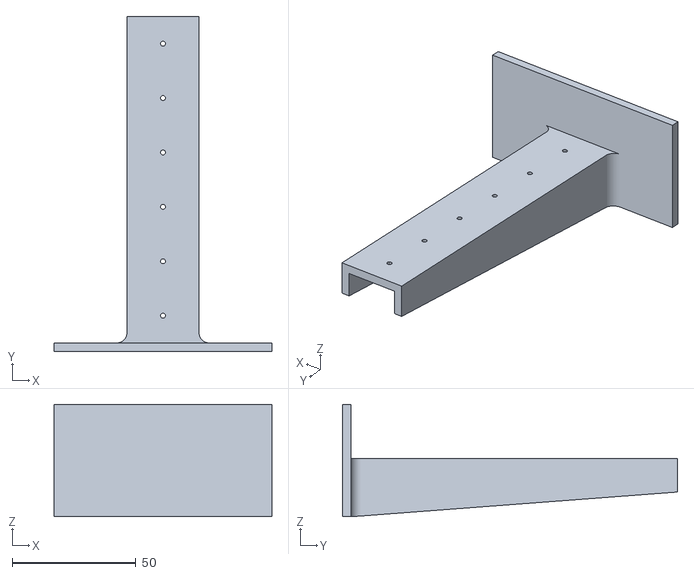
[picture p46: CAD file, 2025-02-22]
src/STL/tools/Hole Drilling Jig.stl
88.0 x 135.5 x 45.5

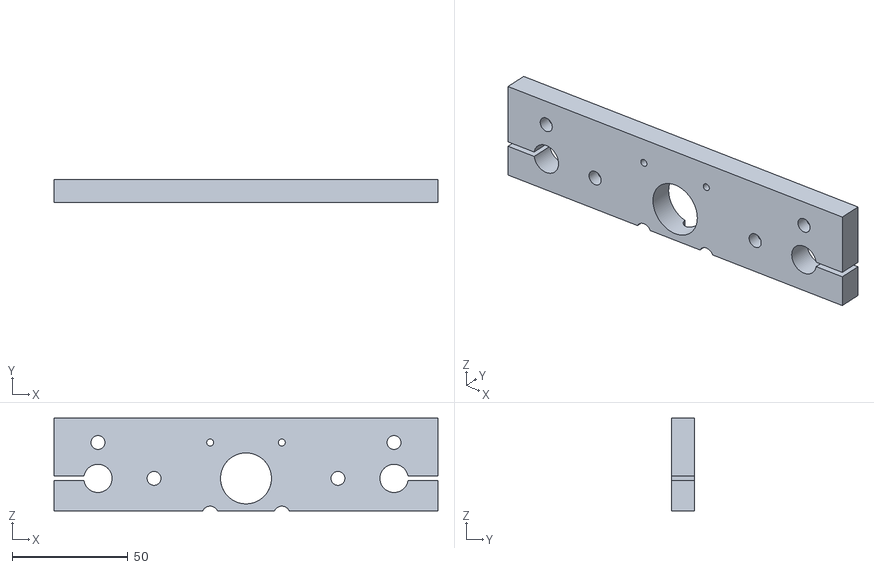
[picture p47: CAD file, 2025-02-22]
src/STL/Y-Axis Rear Mount.stl
166.0 x 10.0 x 40.0

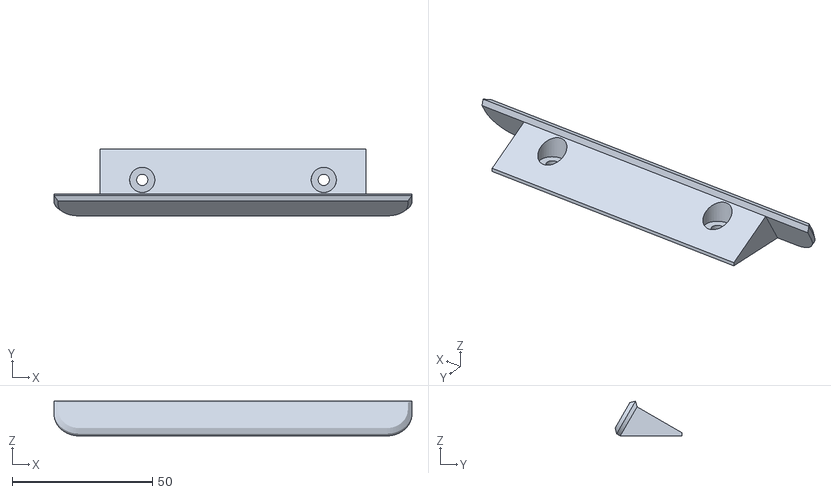
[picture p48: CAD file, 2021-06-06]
src/STL/controlpanel/Bottom.stl
127.8 x 23.8 x 12.4

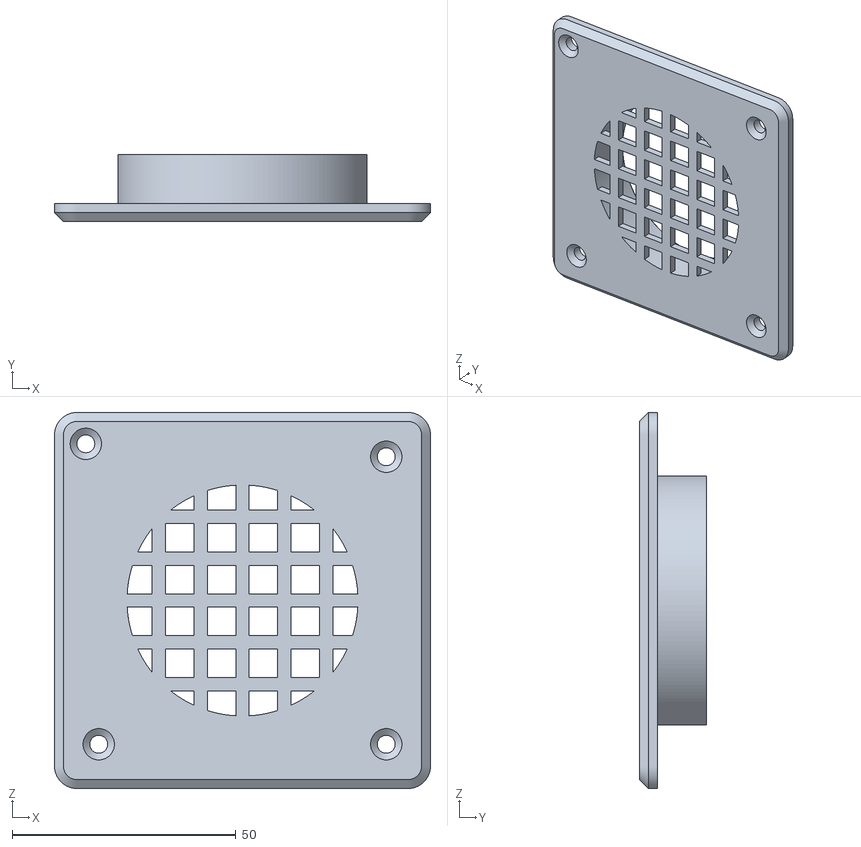
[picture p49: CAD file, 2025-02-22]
src/STL/extras/Vent Cover.stl
84.0 x 15.0 x 84.0

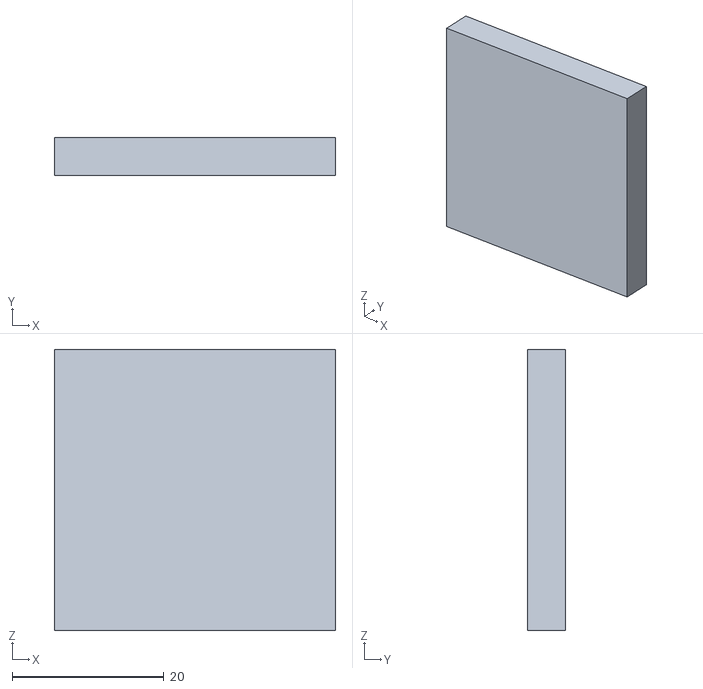
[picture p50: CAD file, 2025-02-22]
src/STL/shims/Y-Axis Alignment Jig.stl
37.0 x 5.00 x 37.0

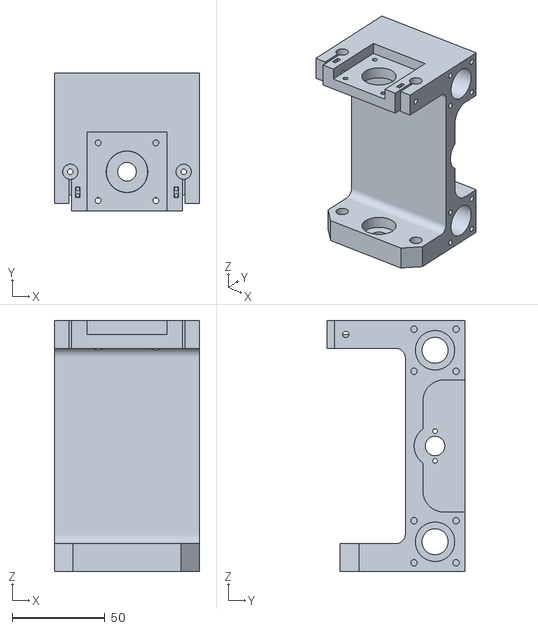
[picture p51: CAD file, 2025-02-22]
src/STL/X-Carriage.stl
78.0 x 74.0 x 135.0

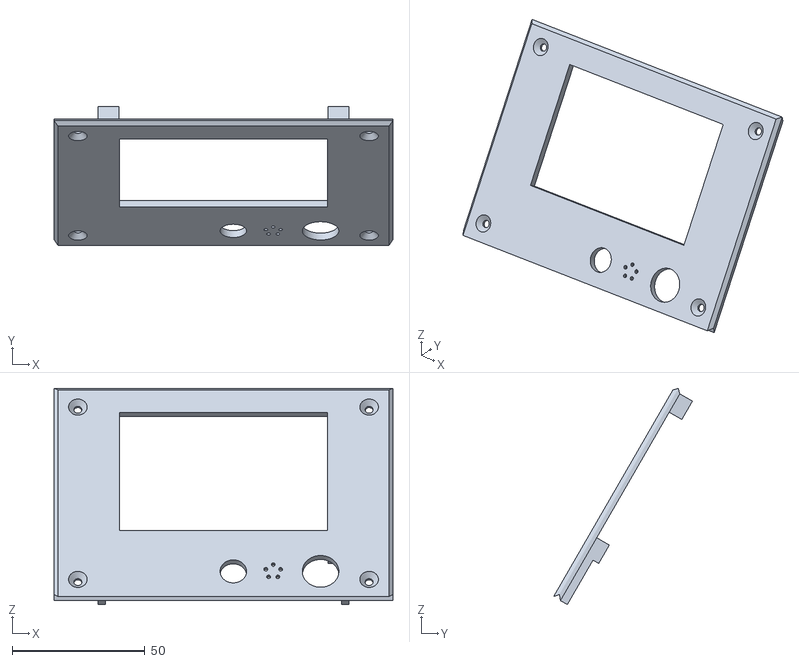
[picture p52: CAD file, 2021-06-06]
src/STL/controlpanel/LCD.stl
127.8 x 52.4 x 81.5

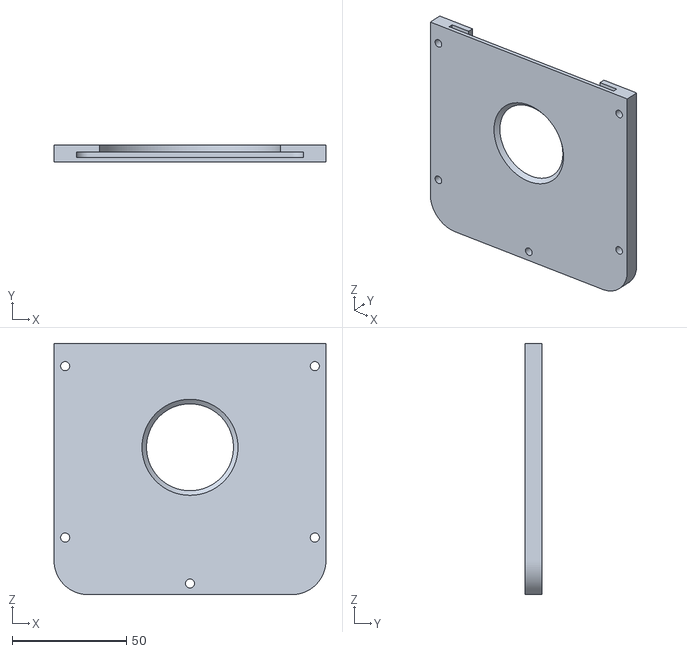
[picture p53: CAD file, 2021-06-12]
src/STL/extras/Vaccum Bag Holder.stl
119.0 x 7.30 x 110.0

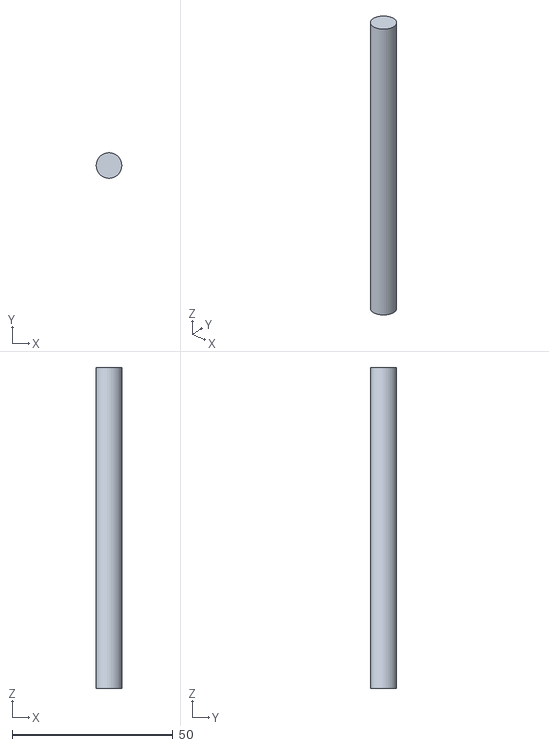
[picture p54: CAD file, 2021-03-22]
src/STL/mocks/8x100mmShaft.stl
8.00 x 8.00 x 100.0

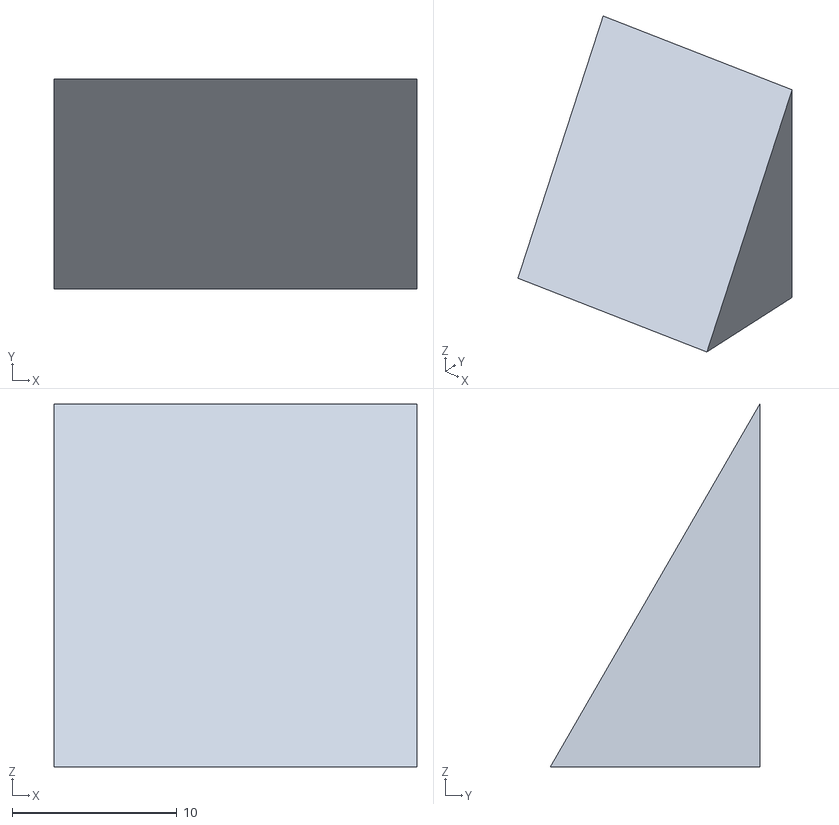
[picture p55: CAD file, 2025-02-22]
src/STL/shims/Top Left Angle Shim.stl
22.0 x 12.7 x 22.0

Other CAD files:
src/STL/Y-Axis Front Mount.stl
src/STL/controlpanel/ResetButtonCap.stl
src/STL/extras/Spindle PSU Din Rail Mount.stl
src/STL/mocks/LMK12UU.stl
src/ERK-1.f3z
src/STL/X-Axis Left Mount.stl
src/STL/X-Axis Right Mount.stl
src/STL/Y-Carriage.stl
src/STL/Z-Carriage.stl
src/STL/controlpanel/E-Stop.stl
src/STL/controlpanel/Top.stl
src/STL/extras/12V PSU DIN Rail Mount.stl
src/STL/mocks/FlexibleCoupling5to8mm.stl
src/STL/mocks/LMK8LUU.stl
src/STL/mocks/LMK8UU.stl
src/STL/mocks/Spindle200W.stl
src/STL/mocks/SpindleClamp52mm.stl
src/STL/mocks/T8 Brass Nut.stl
src/STL/mocks/T8x90mmLeadscrew.stl
src/STL/shims/MidWall Angle Shim.stl
src/STL/shims/Stepper Shim.stl

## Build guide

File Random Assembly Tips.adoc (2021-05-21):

= Yeah

Try to avoid using powertools when screwing into 3D-printed parts. If you must use machine tools, do it slowly, and take breaks. The friction of the screw against the plastic can make things really hot. If you just drive a screw in as fast as you can, you will probably melt the screw hole and ruin the threads. At the very minimuim, take a break and let things cool down, before screwing the last bit. If the threads are melted and soft when you tighten things together, the threads will get destroyed.

The Z-axis stepper motor shaft needs to be shortened to get the rigid coupler sufficiently up and away from the Z-carriage. The shaft is normally about 22mm. Use a dremel or something to shorten the shaft to 15mm. Try to avoid getting metal powder in the bearings of the stepper motor (use masking tape or something while you are cutting).
Be careful when doing this cut so that the stepper motor shaft does not get hot enough to melt the plastic parts inside the stepper motor. Also do not use excessive force that could bend the shaft.
Suggested method:
Use a Dremel with a cutting disk to cut the motor shaft. Put a small moistened strip of paper towel on the shaft while cutting. Reapply water to this whenever the water boils away during cutting. Clean up around the cut with a Dremel polishing or sanding bit. Any bits of metal sticking out to the side will affect the alignment of the motor coupler.

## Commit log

2021-03-18 ## - Started git-blogging!
    [ERK-1.f3d, LMK8UU.stl, Spindle200W.stl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]
2021-03-19 ## - Update 2.
    [FlexibleCoupling5to8mm.stl]
2021-03-19 ## - Adding latest Fusion360 file.
    [ERK-1.f3d, ERK-1.f3z]
2021-03-22 ## - Update 3.
    [8x100mmShaft.stl, FlexibleCoupling5to8mm.stl, LMK12UU.stl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]
2021-03-22 ## - Updated BOM.
2021-03-22 ## - Adding latest Fusion 360 file.
    [ERK-1.f3z]
2021-03-25 ## - Update 4.
    [ERK-1.f3z, X-Carriage_Top.stl]
2021-03-31 ## - Update 6.
    [ERK-1.f3z, X-Carriage_Base.stl, Y-Carriage.stl]
2021-04-04 ## - Update 7.
    [X-Axis Left Mount.stl, X-Axis Right Mount.stl, X-Carriage.stl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]
2021-05-02 ## - Update 8.
    [RigidCoupling5to8mm.stl]
2021-05-16 ## - Update 9.
    [Bottom.stl, E-Stop.stl, PSU DIN Rail Mount.stl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]
2021-05-21 ## - Taking notes about assembly.
2021-06-06 ## - Update 10.
    [Bottom.stl, E-Stop.stl, LCD.stl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]
2021-06-12 ## - Update 11.
    [12V PSU DIN Rail Mount.stl, PSU DIN Rail Mount.stl, Spindle Control.stl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]
2025-02-22 Some more progress.
    [Hole Drilling Jig.stl, MidWall Angle Shim.stl, Top Left Angle Shim.stl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]
